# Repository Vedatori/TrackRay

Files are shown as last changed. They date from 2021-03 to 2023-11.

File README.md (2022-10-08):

# TrackRay [cz]
TrackRay je otevřená platforma robotického vozidla. Byl vyvinut pro [Letní technické soustředění 2020](http://wp.vedatori.com/pobytove-tabory/), které se věnovalo robotice, elektronice, programování a mechanické stavbě. Tábor pořádal spolek [Vědátoři](http://vedatori.com/), hlavními vývojáři byli Martin Ptáček, Martin Coufal a Marek Coufal. Dále se na vývoji podíleli Aleš Kraml, Petr Vávra, Max Matějka a Tomáš Sajdl. Jedná se o pásové vozidlo, které je schopné se pohybovat ve vnitřních prostorech, ale i v mírnějším terénu.

Větší mechanické části jsou vyřezány z překližky a plexiskla na lasové řezačce, spojovací díly a menší části jsou vytištěné na FDM 3D tiskárnách. Spojování dílů je řešeno pomocí šroubů M3. Vozidlo má poháněná zadní kola, k tomu je použit běžně dostupný motor s převodovkou. Všechna kola jsou uložena bez vypružení. Pásy byly navrženy tak, aby je bylo možné vytisknout na 3D tiskárně s již hotovým kloubovým spojením mezi jednotlivými segmenty - tím se minimalizoval počet spojů, které musí být při stavbě zhotoveny.

Elektronika je soustředěna na jednu DPS. Její součástí je i běžně neodebíratelný akumulátor 18650, nabíjecí obvod a indikátor nabití. Do desky se vsazuje mikrokontrolér ESP32-CAM. Ten zajišťuje WiFi konektivitu a ovládání periferií, jako je například LED matice 5x5 určená pro komunikaci s okolím nebo bzučák. TrackRay obsahuje gyroskop, pomocí něhož lze dosáhnout velmi přesné jízdy. Obraz z kamery připojené k mikrokontroléru je přenášen tak, aby ho viděl operátor. 

Vozidlo je možné opakovaně přeprogramovat a periferie jsou zvoleny tak, aby si na nich mohli uživatelé vyzkoušet mnoho úloh, které rozvedou jejich schopnosti algorimizace a programování. Je vytvořen firmware pro dálkové ovládání přes WiFi. Ten umožňuje buďto ovládání pomocí WiFi, kterou vytvoří samotné vozidlo, nebo je možné jej připojit k běžné domácí síti. Ovládání je přizpůsobeno pro chytrá zařízení, na nichž se zobrazí joystick pro jízdu a také obraz přenášený z kamery. Dále je možné zadat speciální příkazy do příkazového řádku, pomocí nich je možné ovládat některé z periferií.

K TrackRay bylo vyvinuto i dělo, které střílí airsoftové kuličky a dřevěné špalíky. Jeho autorem je Jan Cícha.

## Licence
* Obsah tohoto repozitáře mimo složku *Software* je sdílen pod licencí [Attribution-NonCommercial-ShareAlike 4.0 International (CC BY-NC-SA 4.0)](https://creativecommons.org/licenses/by-nc-sa/4.0/).
* Obsah složky *Software* je sdílen pod licencí [GNU Lesser General Public License v3.0](https://www.gnu.org/licenses/lgpl-3.0.en.html).

# TrackRay [en]
TrackRay is an open-source robotic vehicle platform. It was developed for the Robotic Summer Camp 2020 devoted to robotics, electronics, programming and mechanical assembly. The summer camp was organised by the [Vedatori](http://vedatori.com/) association. TrackRay was developed by Martin Ptáček, Martin Coufal and Marek Coufal as main developers, Aleš Kraml, Petr Vávra, Max Matějka and Tomáš Sajdl as associate developers. This vehicle uses tracks that make it capable of both indoor and outdoor driving.

Bigger mechanical parts were laser-cut from plywood and PMMA. FDM 3D printers were used to manufacture smaller parts. The vehicle is assembled using M3 bolts. The rear wheels are driven by standard TT motors, and the tracks are designed to be 3D printed in one piece with joints between each segment. 

All electonic components are placed on a single PCB. It contains 18650 battery with a charger circuit and a charge level indicator. An ESP32-CAM microcontroller is used for WiFi connectivity and peripherals control. A 5x5 LED matrix, a buzzer and a gyroscope are present on the TrackRay PCB. With camera on, it is possible to drive without direct visual contact.

With the used peripherals and option of reprogramming the vehicle it is suitable for gathering new programming skills. Remote control uses WiFi in two modes - if there is no WiFi present, it is possible to use WiFi created by the TrackRay microcontroller. It is also possible to connect TrackRay to a common WiFi network. The control screen is designed for smartphones and contains a joystick to control the robot. A camera stream and a command line to communicate with some of the peripherals.

An airsoft bullet blaster was developed as an optional accessory for the TrackRay. Jan Cícha is main developer of the blaster.

## License
* The contents of this repository excluding folder *Software* is shared under license [Attribution-NonCommercial-ShareAlike 4.0 International (CC BY-NC-SA 4.0)](https://creativecommons.org/licenses/by-nc-sa/4.0/).
* The contents of the folder *Software* is shared under license [GNU Lesser General Public License v3.0](https://www.gnu.org/licenses/lgpl-3.0.en.html).

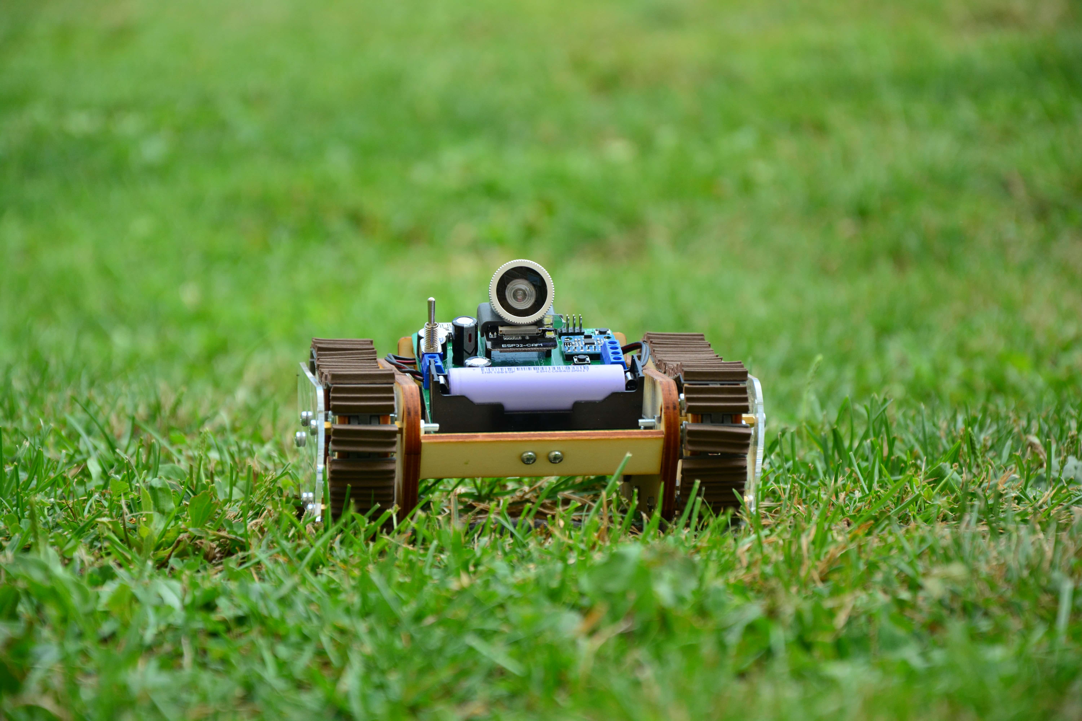
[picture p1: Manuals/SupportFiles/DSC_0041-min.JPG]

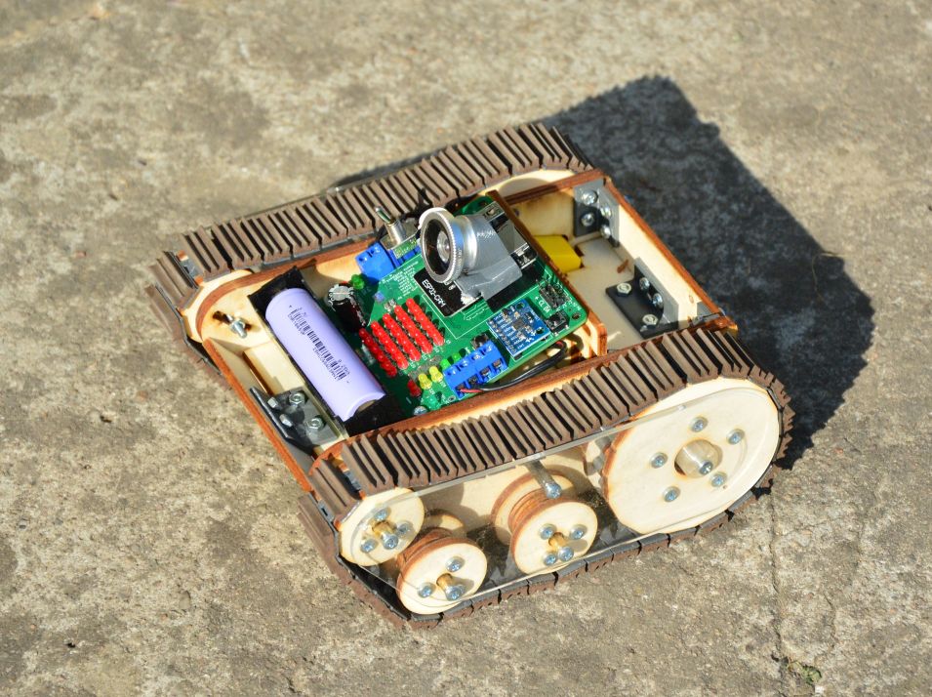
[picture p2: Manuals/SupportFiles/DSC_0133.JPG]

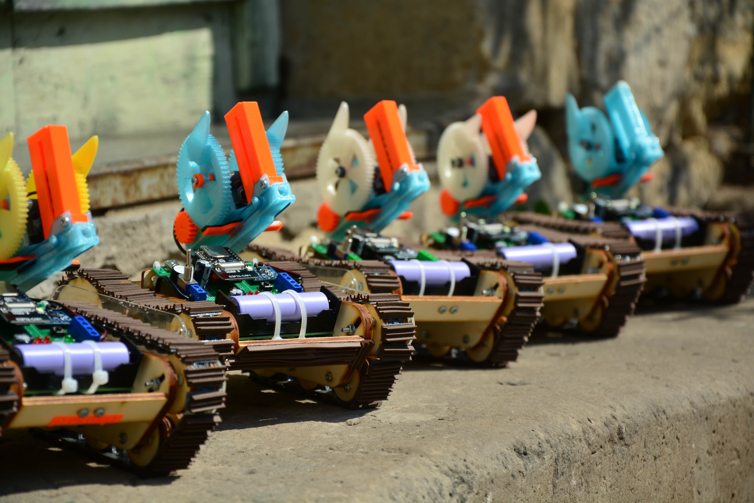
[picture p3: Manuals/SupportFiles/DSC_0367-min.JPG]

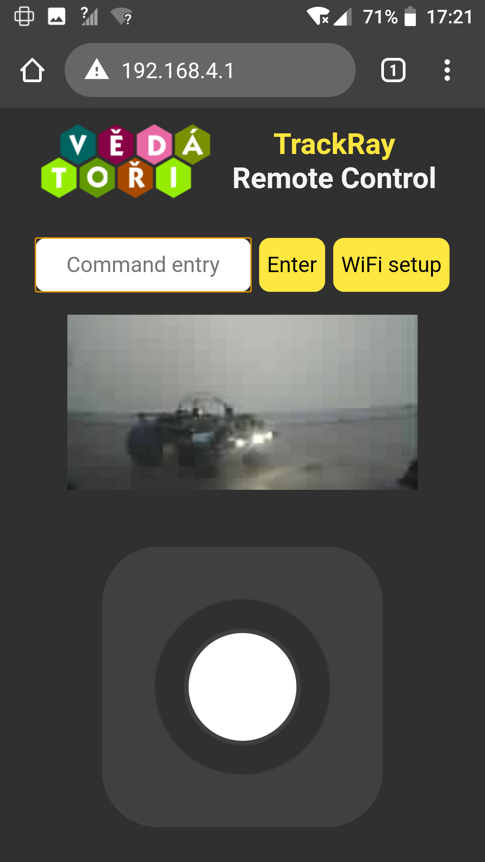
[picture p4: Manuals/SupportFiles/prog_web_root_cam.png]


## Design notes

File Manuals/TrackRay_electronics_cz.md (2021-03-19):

V tomto dokumentu je uveden návod na osazení desky plošných spojů. Část je osazena již z výroby SMD součástkami. Zbytek osazení je předmětem tohoto návodu.
Pro tento návod si uvedeme následující pojmy: DPS = PCB = deska - Deska Plošných Spojů.
Deska pro TrackRay je již z výroby osazena SMD (bezvývodovými) součástkami. THT (vývodové) se pájí následujícím způsobem:
* Součástku vkládáme ze strany, kde je naznačena silkscreenem (kde je bílou barvou natištěn její obrys).
* Součástku přitlačíme až k desce nebo co nejblíž.
* Součástku pájíme ze strany, na kterou trčí vývody.
* Vývody po zapájení zastřihneme.

# Obsah
* [Pájení LED](#LED)
* [Pájení malých součástek](#male)
* [Pájení větších součástek](#vetsi)
* [Vložení desky do robota a propojení](#finalizace)

## <a name = LED>Pájení LED</a>
**Potřebujeme:**
* 28x červená LED
* 4x zelená LED
* 2x žlutá LED

**Postup:**
<span style="color: red;">**POZOR: LED mají definovanou polaritu!**</span> U každé LED zkontrolujte, že kratší nožku vsouváte do čtveraté díry! 
1. Do desky vložte LED tak, aby barvy odpovídaly LED na obrázku. 
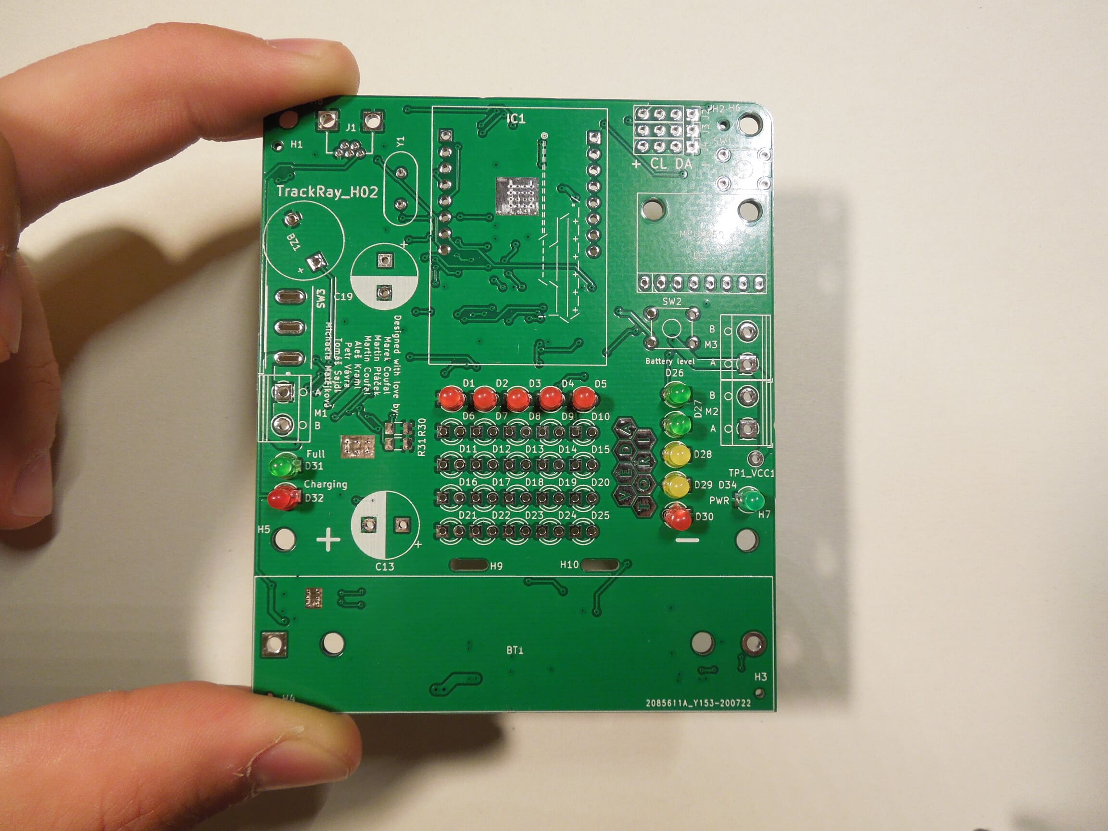
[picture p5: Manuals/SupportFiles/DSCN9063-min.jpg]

1. Na LED nasaďte pájecí přípravek. 
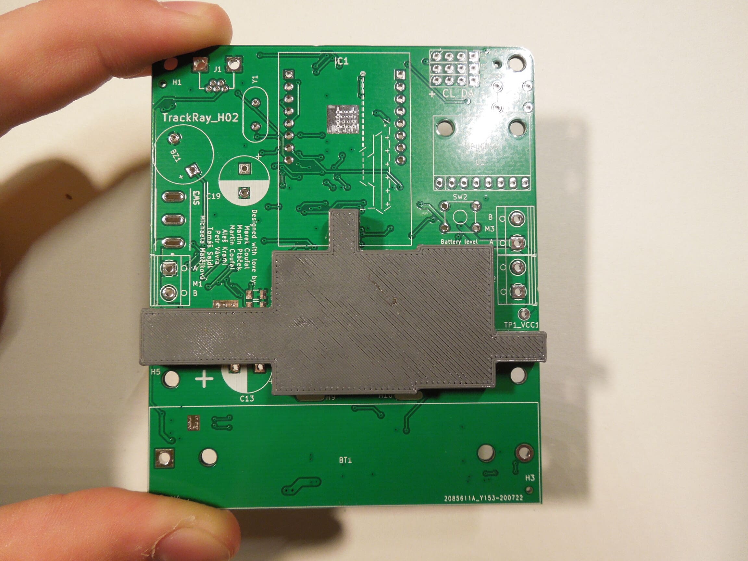
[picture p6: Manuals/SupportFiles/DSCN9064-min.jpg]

1. <span style="color: red;">**Před dalším postupem si nechte zkontrolovat desku vedoucím!**</span>
1. Vývody vsazených LED zapájejte. 
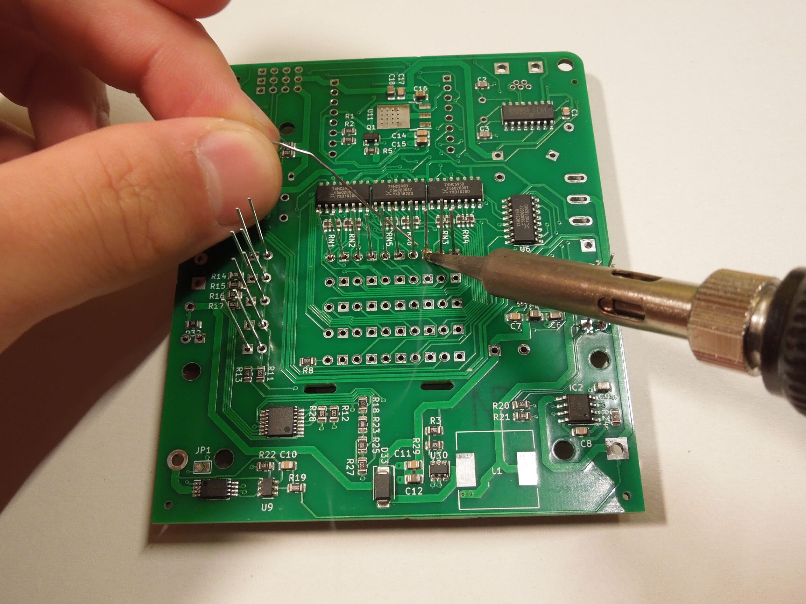
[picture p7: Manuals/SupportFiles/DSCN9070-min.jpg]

1. Do pole vložte další řadu LED. 
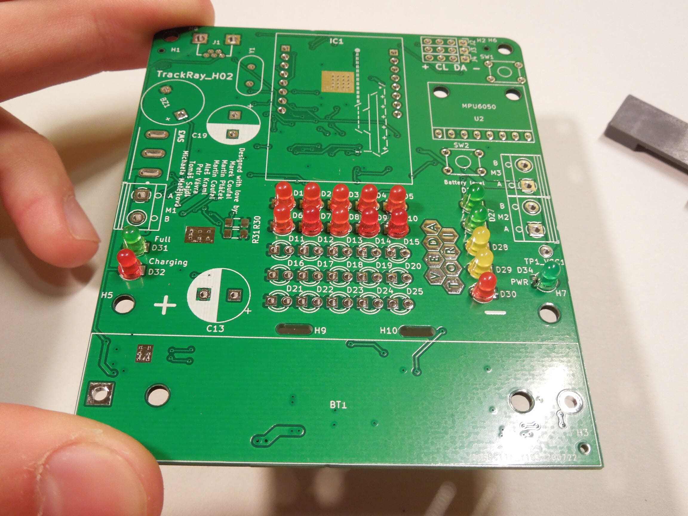
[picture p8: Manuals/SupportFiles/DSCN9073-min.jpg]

1. Nasaďte přípravek.
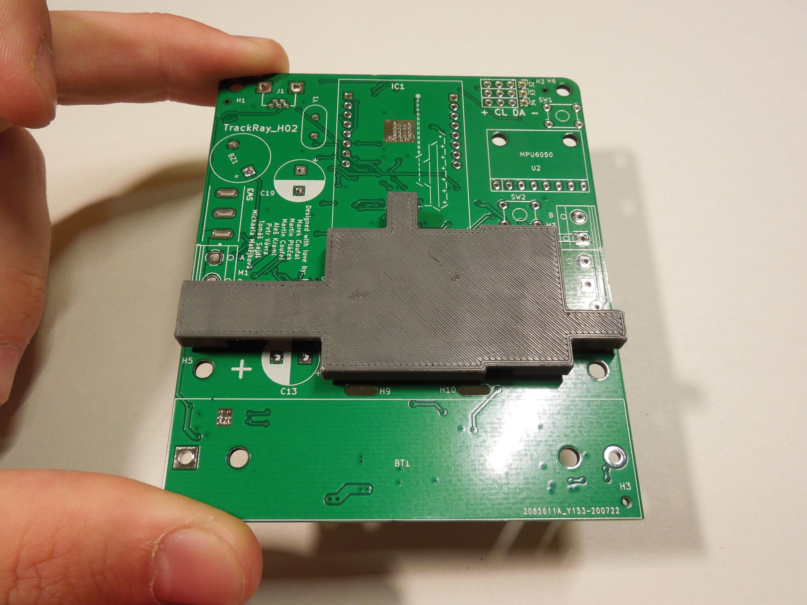
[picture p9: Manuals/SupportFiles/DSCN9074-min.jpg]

1. Zapájejte novou řadu LED.
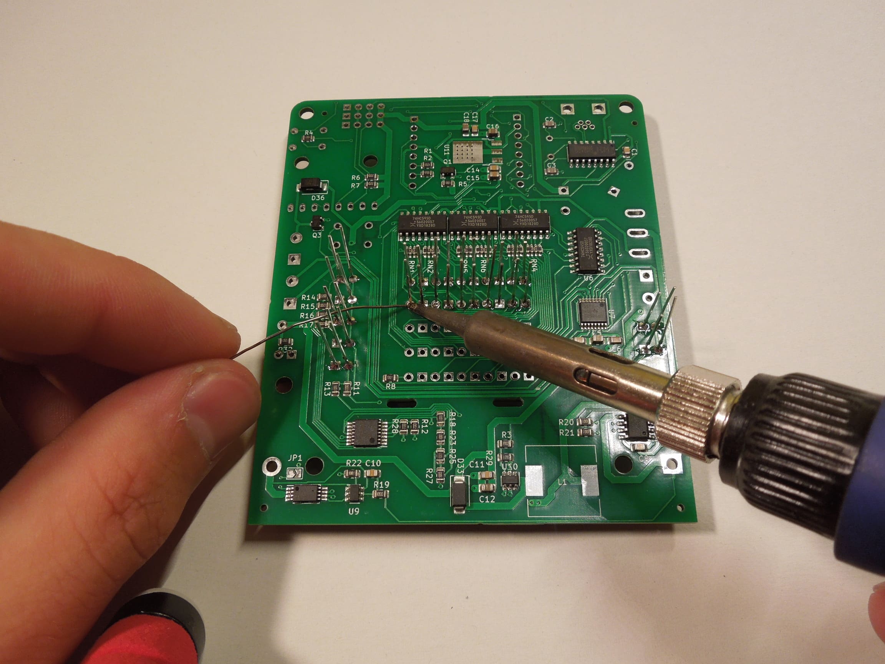
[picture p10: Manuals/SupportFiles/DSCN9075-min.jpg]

1. Tento postup opakujte, dokud nebudou zapájené všechny LED. 
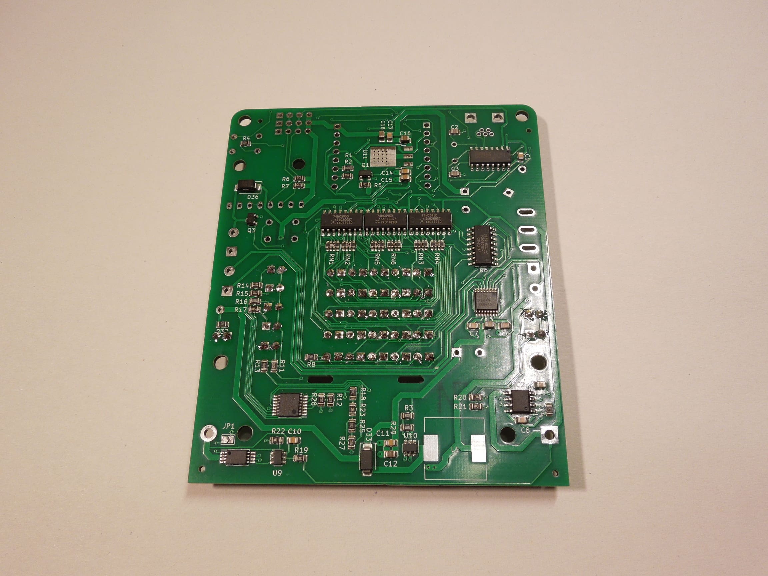
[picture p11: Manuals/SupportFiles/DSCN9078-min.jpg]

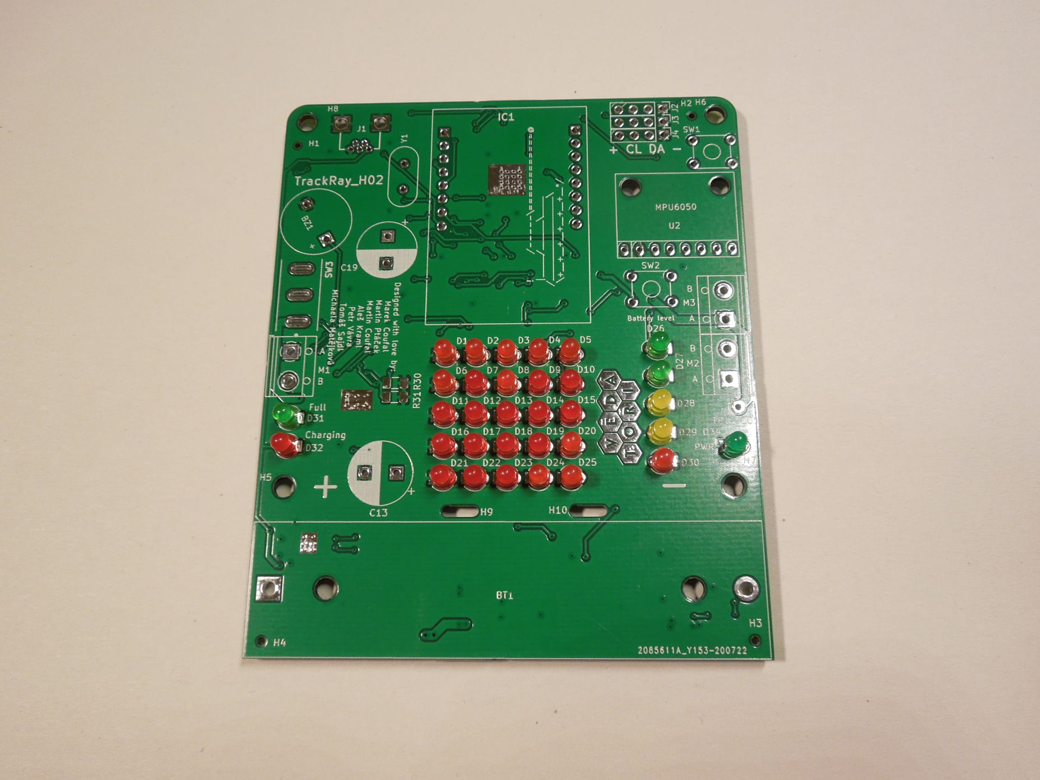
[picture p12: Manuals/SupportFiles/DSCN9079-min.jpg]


## <a name = male>Pájení malých součástek</a>
**Potřebujeme:**
* 2x SMD rezistor 0,22 Ohm
* 1x USB konektor
* 1x krystal
* 2x tlačítko

**Postup:**
1. Zapájejte *jumper JP1* na spodní straně desky a spojte cínem obě jeho plošky.
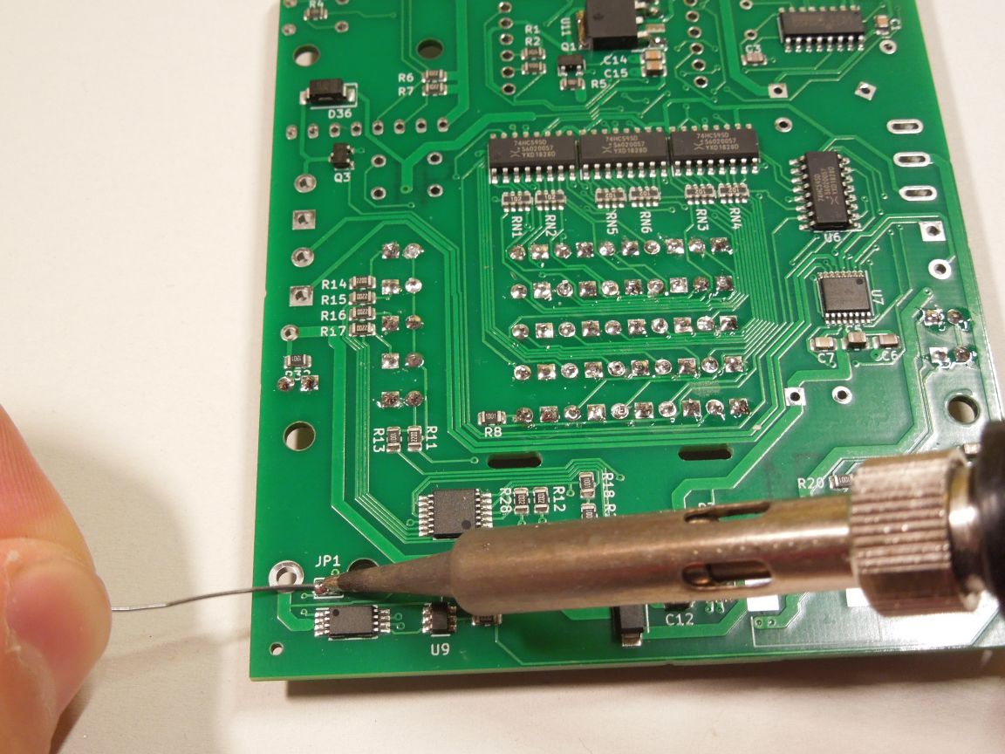
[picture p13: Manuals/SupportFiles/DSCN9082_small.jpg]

1. Zapájejte SMD rezistory. Na jednu pájecí plošku naneste pájku.
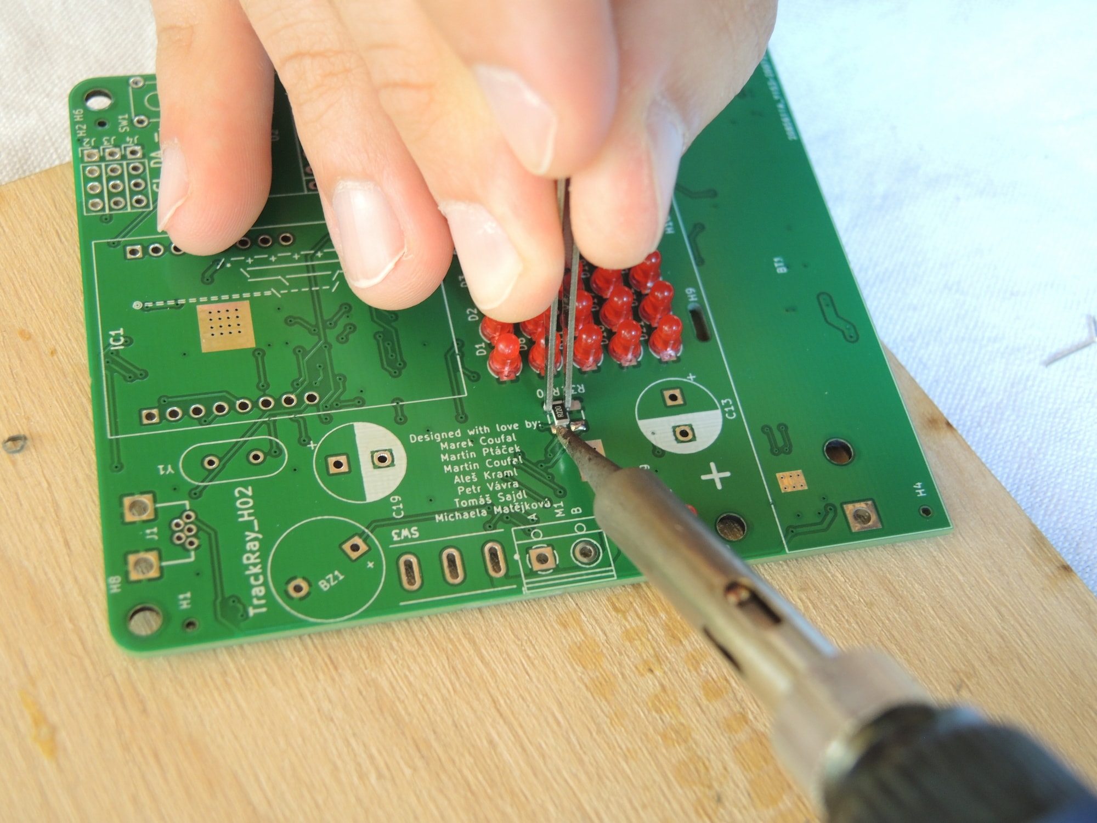
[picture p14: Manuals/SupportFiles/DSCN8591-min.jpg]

1. Přiložte SMD rezistor. Roztavte předem nanesený cín a tím připájejte rezistor. Poté zapájejte druhý vývod rezistoru. Stejným způsobem zapájejte i druhý rezistor.
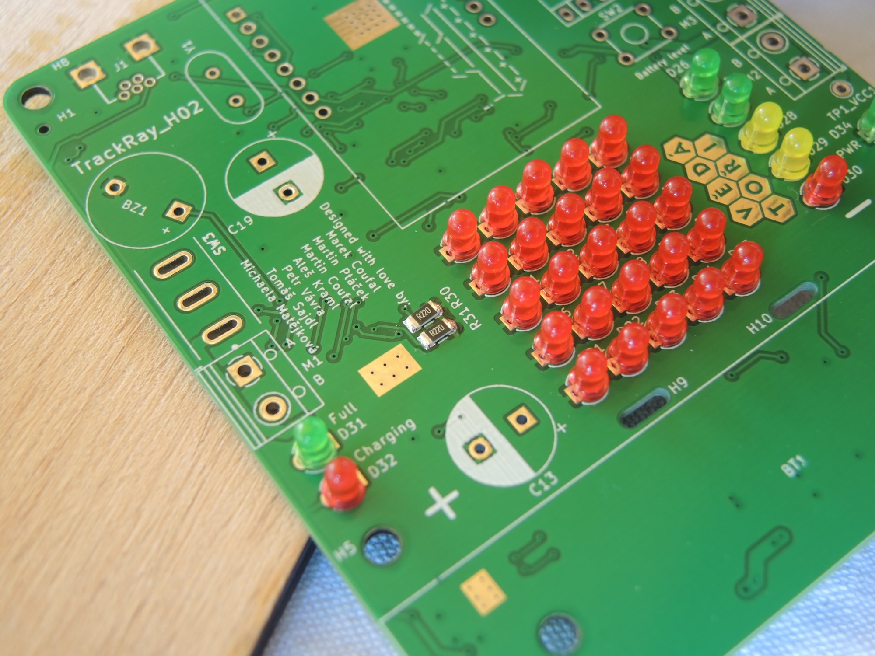
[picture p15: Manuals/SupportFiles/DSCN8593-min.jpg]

1. Vložte USB konektor na místo H8. Skrz desku musí vyčnívat tenké vývody i tlusté fixovací vývody.
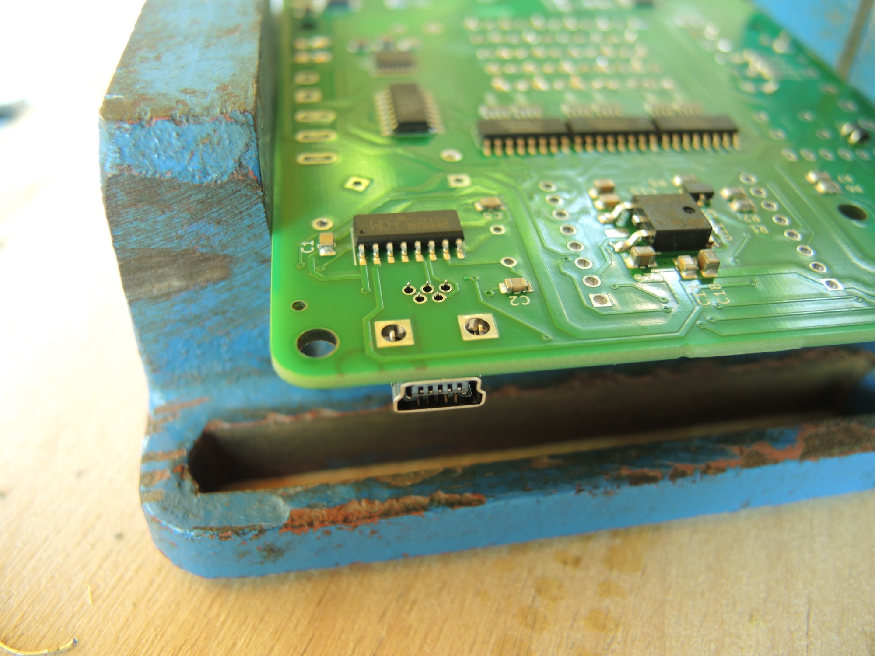
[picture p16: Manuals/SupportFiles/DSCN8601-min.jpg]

1. Tlusté i tenké vývody připájejte klasicky zespodu, jak je popsáno v úvodní části návodu. Tlusté vývody je možné zapájet z obou stran. 
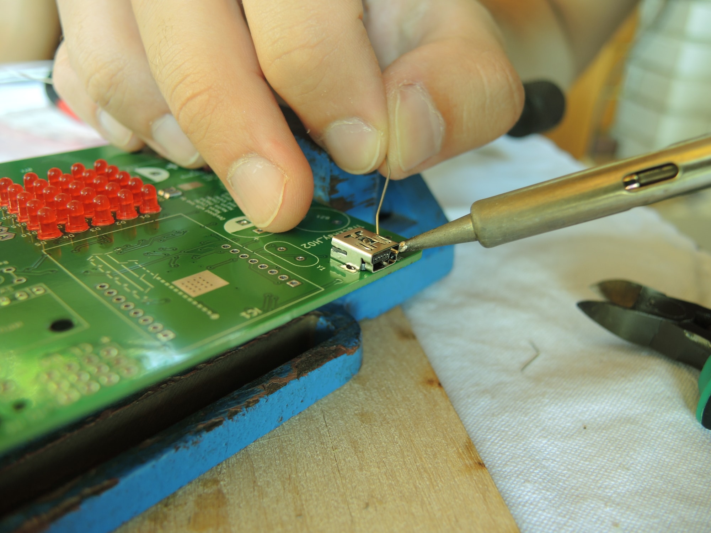
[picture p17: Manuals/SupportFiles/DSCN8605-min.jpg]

1. Na místo Y1 zapájejte krystal.
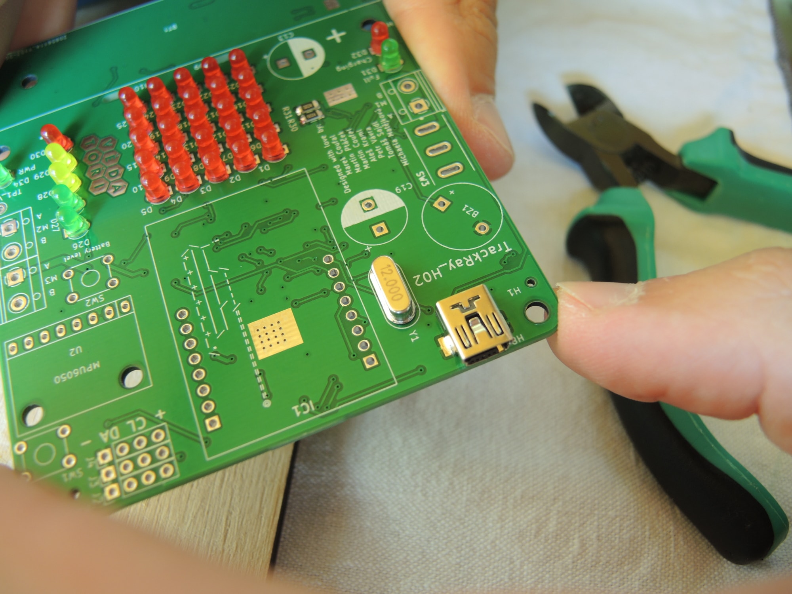
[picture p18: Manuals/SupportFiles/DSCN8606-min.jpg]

1. Na místa SW1 a SW2 zapájejte tlačítka. 
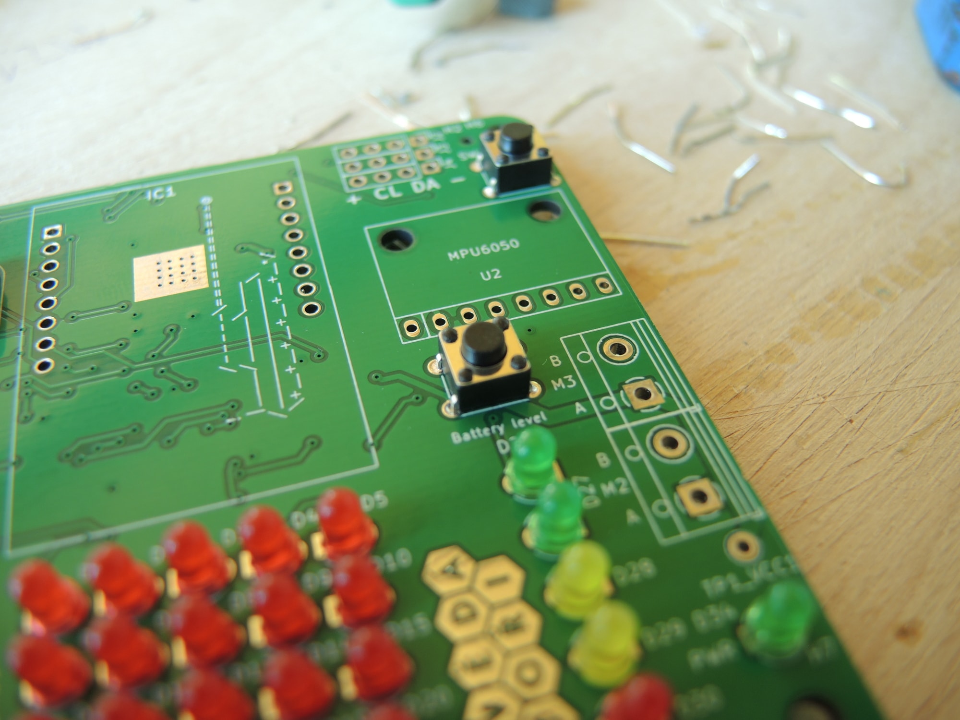
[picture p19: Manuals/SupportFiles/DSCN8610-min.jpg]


## <a name = vetsi>Pájení větších součástek</a>
**Potřebujeme:**
* 0,5x dutinková lišta
* 3x terminal block
* 2x elektrolytický kondenzátor 1000 uF
* 1x páčkový přepínač
* 1x držák baterie
* 1x gyroskop

**Postup:**
1. Naměřte si dutinkovou lištu tak, abyste si vyrobili 2x 8pin dutinky. Dutinky oddělte kleštěmi vždy uprostřed dalšího pinu, ten se zničí.
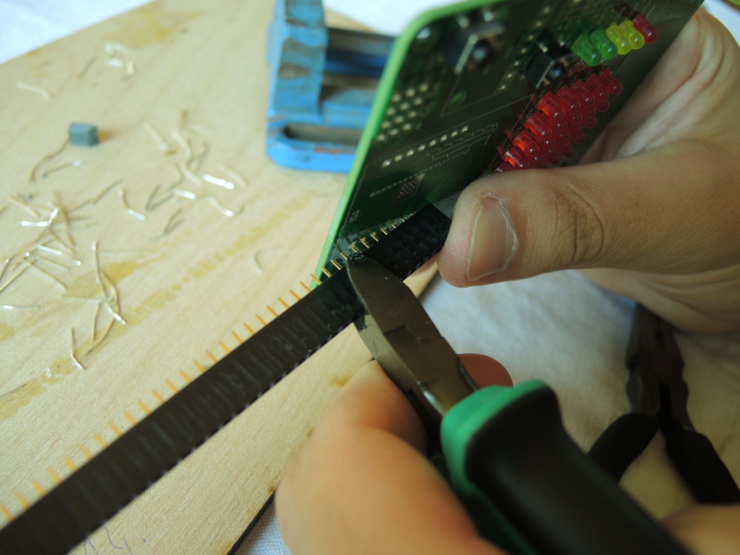
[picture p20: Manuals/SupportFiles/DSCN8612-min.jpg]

1. Nadělené dutinky začistěte nožem nebo kleštěmi tak, aby nebyly viditelné zbytky odstřihnutého pinu.
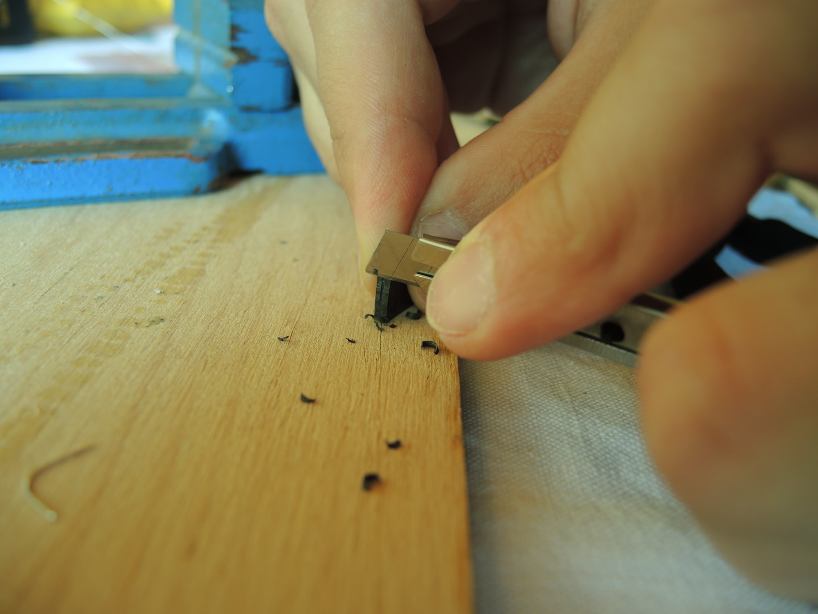
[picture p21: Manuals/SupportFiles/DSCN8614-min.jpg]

1. Vložte dutinku do desky k umístění IC1, zapájejte jeden pin. Poté zkontrolujte, jestli není dutinka nakřivo. Dorovnejte a zapájejte ostatní piny.
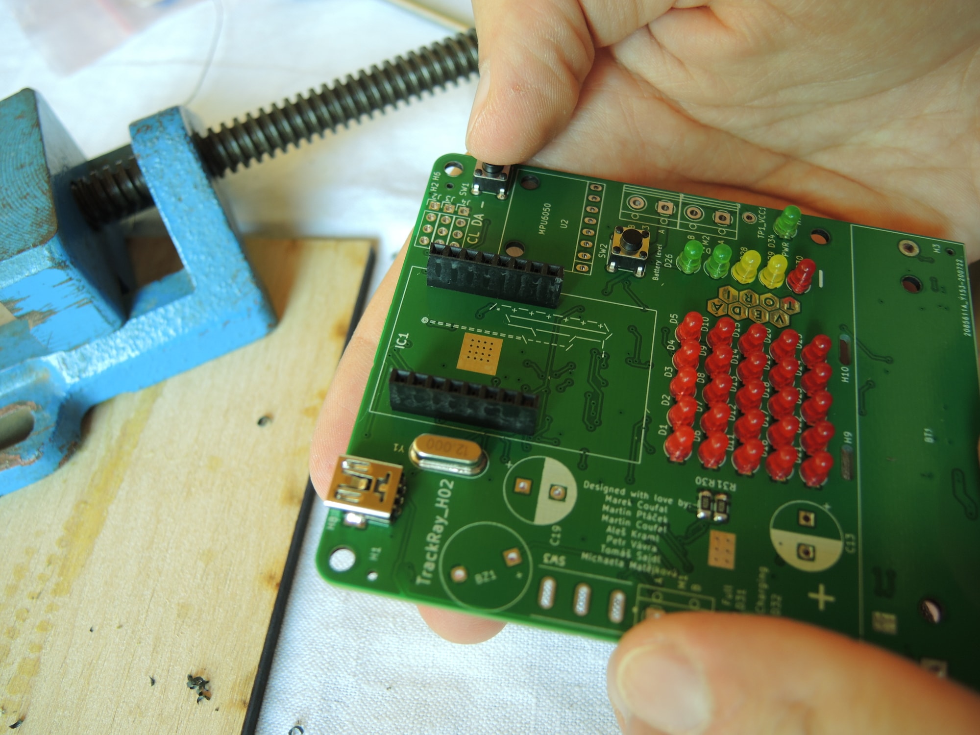
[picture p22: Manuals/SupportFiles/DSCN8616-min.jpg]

1. Zapájejte buzzer do místa s označením BZ1. Pozor na polaritu, delší vývod (u symbolu plus na etiketě buzzeru) musí být umístěn do otvoru označeným symbolem +. 
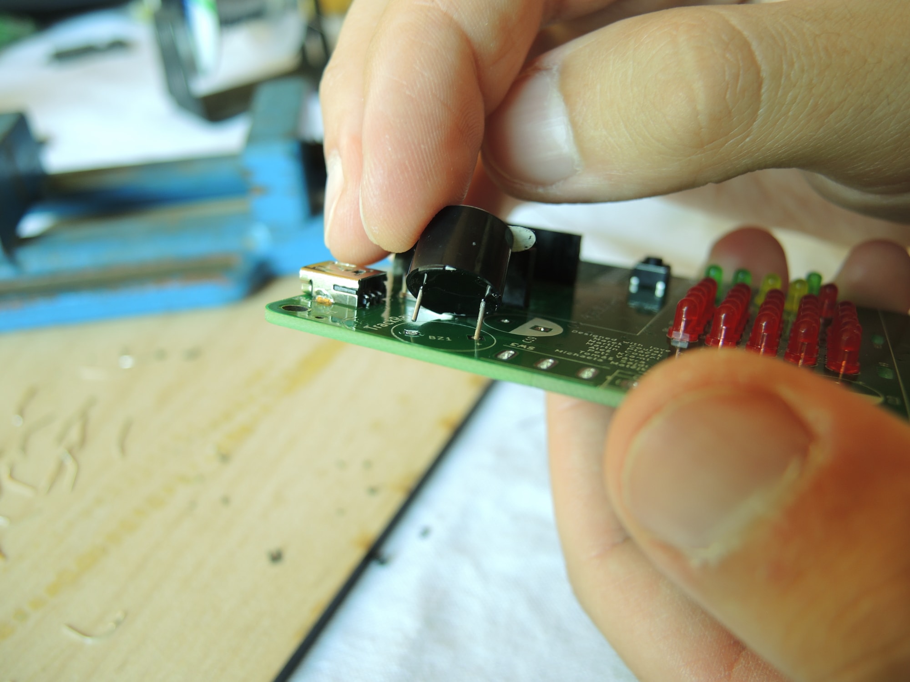
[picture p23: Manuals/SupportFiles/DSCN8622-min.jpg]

1. Nasuňte do sebe dva terminal blocky. 
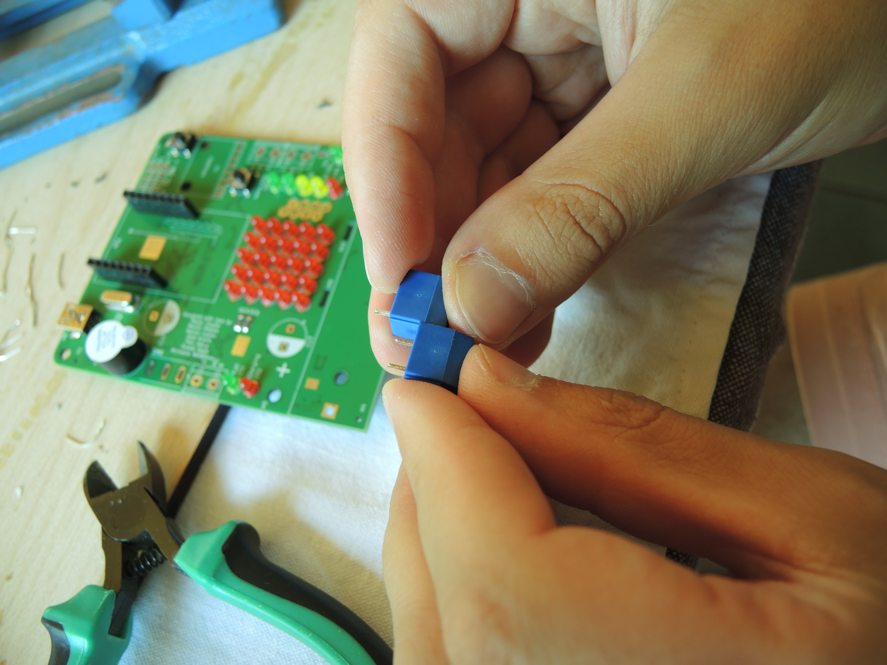
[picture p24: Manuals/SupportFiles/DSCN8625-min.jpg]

1. Zapájejte je na místa označená M2 a M3 tak, aby otvory pro kabely směřovaly ven z desky. 
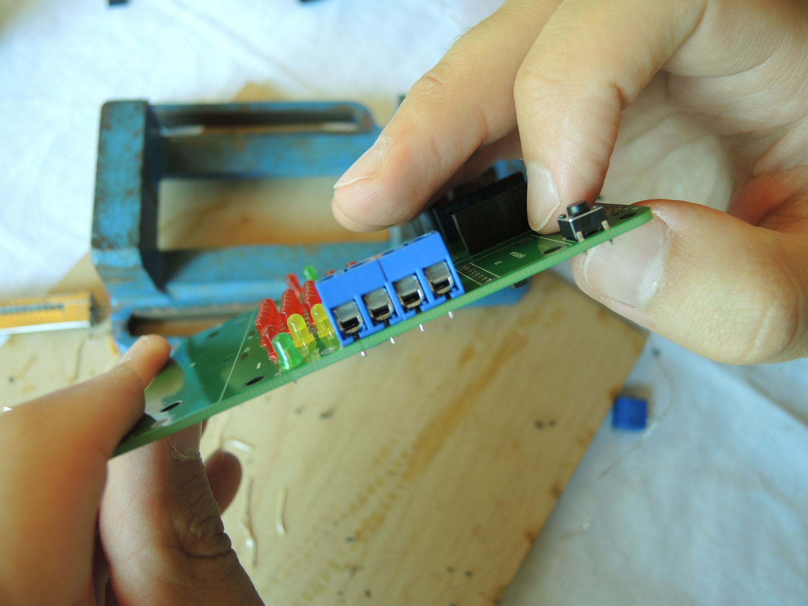
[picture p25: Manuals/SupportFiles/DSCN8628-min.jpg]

1. Zapájejte jeden terminal block na místo M1 tak, aby otvory pro kabely směřovaly ven z desky. 
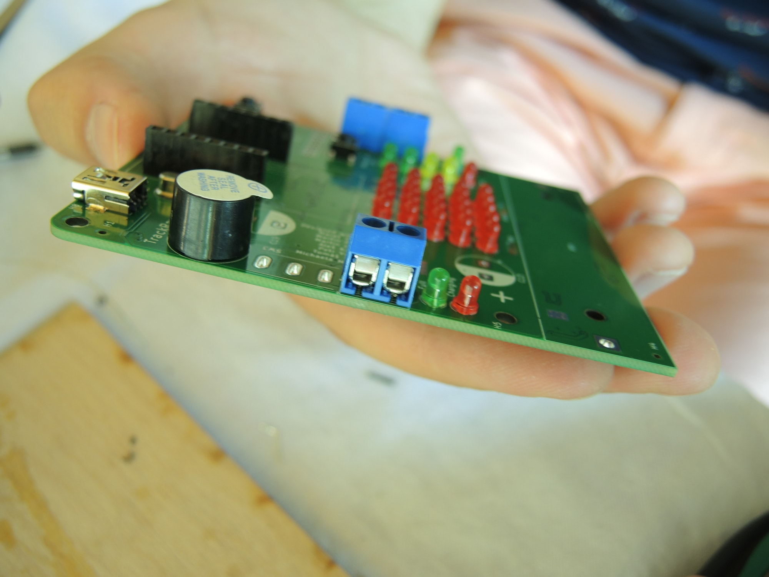
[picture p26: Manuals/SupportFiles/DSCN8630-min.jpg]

1. Na místa označená C13 a C19 zapájejte elektolytické kondenzátory. Pozor na polaritu, delší vývod musí směřovat do otvoru, u kterého je smybol + a jeho okolí není zabarvené bílou barvou.
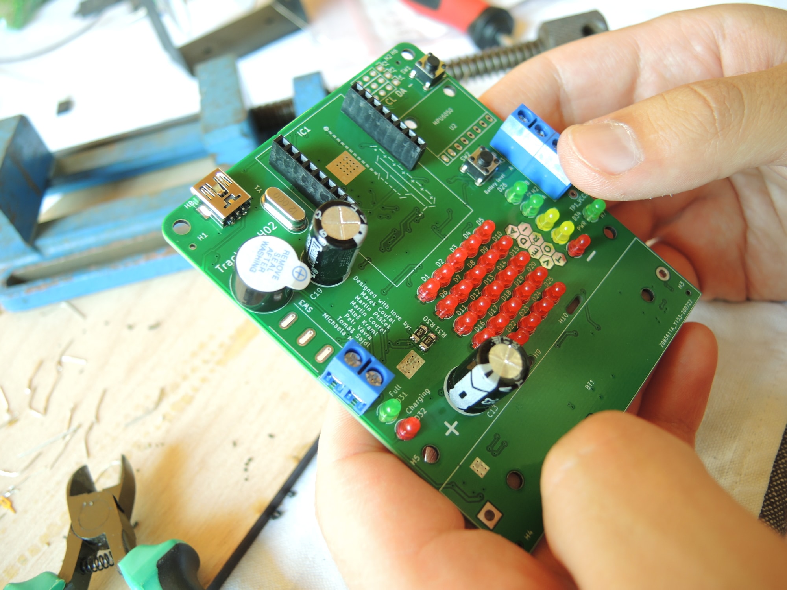
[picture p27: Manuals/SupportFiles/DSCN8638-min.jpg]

1. Na místo označené SW3 vložte páčkový přepínač. Zapájejte. Při pájení dbejte na to, aby byl kolmo k desce, po připájení je obtížné ho narovnat. 
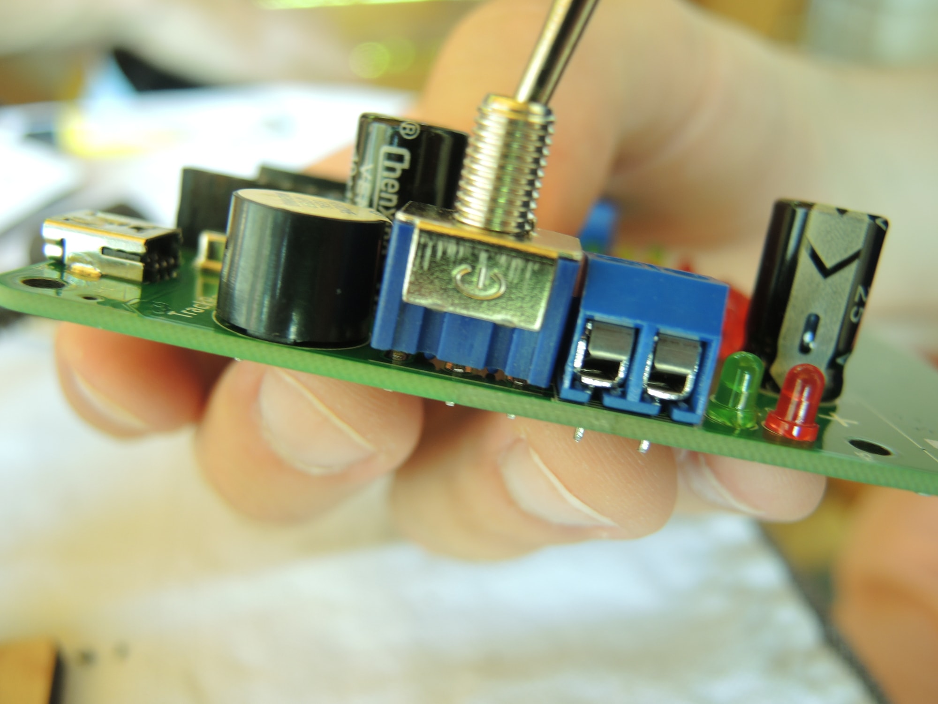
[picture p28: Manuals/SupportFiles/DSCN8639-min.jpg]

1. Na místo označené BT1 připájejte držák baterie. Symbol + na desce musí odpovídat symbolu + na držáku baterie. 

1. Napájejte kolíkovou lištu na gyroskop. Nejdříve zapájejte jeden pin a poté lištu srovnejte, aby s deskou gyroskopu svírala pravý úhel. Poté zapájejte ostatní piny kolíkové lišty.

1. Zapájejte gyroskop do desky na místo označené MPU6050. 


## <a name = Finalizace>VLožení desky do robota a propojení</a>
**Potřebujeme:**
* 2x šroub M3x8
* 2x velký upínací pásek
* 2x malý upínací pásek

**Postup:**
1. Baterii do robota vsazuje vedoucí!!! Po jejím vsazení ji přichyťte pomocí velkých upínacích pásků, jejich konce zastřihněte kleštěmi.


1. Desku vložte do robota. Pomocí dvou šroubů M3x8 desku zašroubujte do držáků na robotovi skrz díry H5 a H7 na desce. 

1. Do terminal blocků M1 a M2 připojte kabely od motorů. Kabel s červeným proužkem bude vždy připojen do otvoru blíže baterii. Zašroubujte.

1. Na horní straně desku připevněte skrz díry H1 a H6 pomocí upínacích pásků. Zcela je nedotahujte. Konce zastřihněte. 



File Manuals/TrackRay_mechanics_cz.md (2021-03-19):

V tomto dokumentu je uveden návod na sestavení mechanických dílů vozítka TrackRay. Část mechanických dílů je vyrobena technologií 3D tisku, část je vyřezána z překližky a plexiskla pomocí laseru, dalším dílem je osazená deska plošných spojů, ostatní součástky tvoří běžně dostupný spojovací materiál. 

___
# Obsah
* [Příprava překližkových dílů](#preklizka)
* [Sestavení velkých kol](#kolo)
* [Sestavení malých kol](#kolecka)
* [Sestavení bočnic #1](#bocnice1)
* [Sestavení bočnic #2](#bocnice2)
* [Kompletace šasi](#sasi)
* [Polepení pásů](#pasy1)
* [Slepení pásů](#pasy2)
* [Nasazení pásů](#pasy3)
* [Kamera](#kamera)
___

## <a name = preklizka>Příprava překližkových dílů</a>
**Nástroje:**
* Smirek

**Postup:**
1. Obruste smirkem všechny nedořezky. 


## <a name = kolo>Sestavení velkých kol</a>
**Potřebné díly:**


* 2x kolo neozubené velké z překližky
* 1x kolo ozubené velké z překližky
* 1x kolo ozubené velké 3D tisk
* 5x matice M3
* 5x šroub M3x22

**Nástroje:**
* Křížový šroubovák
* Maticový klíč



**Postup:**
1. Provléct šroub skrz díru pod malou dírkou. Otočit na opačnou stranu. 

    
1. Navléct ozubené kolo z překližky. Malé dírky musí padnout na sebe. 

    
1. Navléct 3D tištěný díl tak, aby výstupek pro zastrčení osy směřoval směrem od dřevěných dílů. 

    
1. Navléct neozubené kolo z překližky. 

    
1. Zašroubovat matku. Neutahovat.

    
1. Doplnit zbylé šrouby a matky. Díly vystředit vůči sobě. Všechny matky utáhnout maticovým klíčem. 

    
1. Celý postup zopakujeme pro druhé kolo.

    
## <a name = kolecka>Sestavení malých kol</a>
**Potřebné díly:**


* 2x kolo neozubené malé z překližky
* 2x kolo neozubené maličké z překližky
* 1x vymezovač kola 3D tisk
* 3x matice M3
* 3x šroub M3x22

**Nástroje:**
* Křížový šroubovák
* Maticový klíč

**Postup:**
1. Provléct šroub skrz malé kolo. 

    
1. Navléct maličké kolečko.

    
1. Navléct další maličké kolečko. 

    
1. Doprostřed vložit vymezovač kola z 3D tisku. 

    
1. Navléct malé kolo. 

    
1. Zašroubovat matku. Neutahovat. 

    
1. Doplnit zbylé šrouby a matky. Díly vystředit vůči sobě. Všechny matky utáhnout. 

    
1. Stejným postupem sestavit zbylá kola. Celkově jich bude 6. 

    

## <a name = bocnice1>Sestavení bočnic #1</a>
**Potřebné díly:**
* 2x bočnice z překližky
* 2x plastový držák z 3D tisku
* 4x matice M3
* 4x šroub M3x10

**Nástroje:**
* Křížový šroubovák
* Maticový klíč
* Klíč na distanční sloupky (šedý)



**Postup:**
1. Rozchystat součástky podle nákresu. 

    
1. Umístit držák na Bočnici 2. 

    
1. Skrz Bočnici 2 provléct šrouby a utáhnout matky. 

    
1. Postup zopakujte pro Bočnici 1. 

    

## <a name = bocnice2>Sestavení bočnic #2</a>
**Potřebné díly:**

Díly jsou uvedeny postupně pro každý krok. 

**Nástroje:**
* Křížový šroubovák
* Maticový klíč
* Klíč na distanční sloupky (šedý)

**Postup:**

*Postup je předveden na Bočnici 2*
1. Odlepit z obou stran plexiskla ochranou folii. 

    
1. Rozchystat součástky podle nákresu. 

    
1. Prošroubovat šroub M3x10 skrz bočnici z plexiskla do distančního sloupku M3x30. 

    
1. Protáhnout šrouby M3x40 skrz bočnici z plexiskla. 

    
1. Na šrouby našroubovat distanční sloupky M3x10. Dotáhnout pomocí klíče na distanční sloupky. 

    
1. Přidat šroub M3x45 do pohyblivé drážky a našroubovat distanční sloupek. Nedotahovat, nechat volně. 

    
1. Nasadit kolečka. 

    
1. Našroubovat distanční sloupky. 

    
1. Dotáhnout distanční sloupky u šroubů M3x40 (jsou v kulatých dírách, ne v pohyblivé drážce). 

    
1. Zatlačte matku šroubovákem do dílu z 3D tisku. 

    [alt](SupportFiles/DSCN8417.JPG)
1. Připravte díly dle obrázku. 

    
1. Připevněte šroubem M3x12. 

    
1. Nasuňte motor do otvoru. Zkontrolujte, že máte vše ve shodě s obrázkem. 
    * Bočnici s 3D tištěným dílem.
    * Kabel jde na opačnou stranu bočnice. 
    * Uštípnutý bílý plast na motoru.

    
1. Zkontrolujte, že máte ve shodě s obrázkem. 

    
1. Nasaďte 3D tištěný díl. Obraťte na druhou stranu. 

    
1. Vložte šrouby M3x25 hlavou k motoru. Obraťte na druhou stranu. 

    
1. Přidejte matky a dotáhněte tak, aby nepraskl plastový kryt motoru.

    
1. Protáhněte šroubky M3x10 hlavou K 3D tištěnému držáku. Obraťte na druhou stranu. 

    
1. Přišroubujte matky a utáhněte. 

    
1. Pro upevnění motoru si připravte tyto díly. 

    
1. Vložte podložku z 3D tisku pod očko od motoru. Obraťte na opačnou stranu.  

    
1. Protáhněte šroub M3x16 s vnořenou hlavou. 

    
1. Našroubujte matku a utáhněte. Hlava šroubu by měla být úplně nebo skoro vyrovnaná s plochou bočnice.

    
1. Pro upevnění hnacího kola budete potřebovat tyto díly. Nasaďte kolo na bílý plast motoru. 

    
1. Prošroubujte středem kola černý vrut 2,2x10 a utáhněnte. 

    
1. Protáhněte kabely od motoru na opačnou stranu bočnice. 

    
1. Pro připevnění L - držáku korby budete potřebovat tyto díly. 

    
1. Umístěte držák a protáhněte šrouby M3x10. Otočte na druhou stranu. 

    
1. Přišroubujte matky, utáhněte. 

    
1. Přiložte obě části bočnice. 

    
1. Přichystejte 3 matky M3 a šroub M3x10. Šroub namontujte a utáhněte.

    
1. Matku v posuvné drážce nedotahujte, kolo nechte volně pohybovat. Další matky utáhněte.

    
1. Stejným postupem zkompletujte druhou bočnici. 

    

## <a name = sasi>Kompletace šasi</a>

**Potřebné díly:**


* Zbývající díly z překližky
* 20 matic
* 20 šroubů M3x8

**Nástroje:**
* Křížový šroubovák
* Maticový klíč

**Postup:**
 
 *Šroubovat a utahovat.* **Dodržujte umístění hlav a konců šroubů podle fotek.**

1. Přišroubujte šasi k bočnici. 

    

    

    

    
1. Stejně na druhé straně. 

    
1. Připevněte L - držák z 3D tisku.

    
1. Připevněte zadní kryt korby.

    
1. Připevněte šikmý držák z 3D tisku (tento držák není pod úhlem 90°).

    
1. Připevněte přední kryt korby. 

    
1. Připevněte L - držák z 3D tisku na přepážku z překližky.

    
1. Spojte přepážku s šasi.

    
1. Nachystejte 3D tištěně držáky desky plošných spojů, 2 šrouby M3x8 a 4 matky M3. Matky vložte do 3D tištěných dílů.

    
1. Spojte držáky s šasi.

    

## <a name = pasy1>Polepení pásů</a>

**Potřebné díly:**
* 4x vytištěný kus pásu
* 2 m těsnění do oken
 
**Nástroje:**
* štípací kleště / nůžky
* 3D tištěné měřidlo



**Postup:**

1. Nastříhejte z pryžové pásky nálepku na každý článek pásu. Bude potřeba 72 kusů těsnění. Použijte 3D tištěné měřítko pro odměření velikosti článků. 

    
1. Každý článek pásů polepte. Na těsnění je pod ochrannou fólií samolepící vrstva.

    

## <a name = pasy2>Slepení pásů</a>

**Potřebné díly:**
* 4x 3D tištěné pásy
* kus filamentu
 
**Nástroje:**
* lepidlo na plasty
* nůžky
* kleště
* pravítko

**Postup:**

1. Nastříhejte z filamentu 4 kusy po 0,9 cm.

    
1. Pomocí kleští vsuňte kus filamentu na spojnici mezi pásy.

     
1. Zalepte kus filamentu z obou stran. **Pozor:** Použijte malé množství lepidla, aby se nedostalo do kloubů pásu.

    
1. Lepidlo nechte zaschnout  min. 20 minut. Po tuto dobu s pásy výrazně nehýbejte, nesnažte se je nasadit na robota!

## <a name = pasy3>Nasazení pásů</a>

**Potřebné díly:**
* 2x zkompletované pásy
* 1x zkompletované šasi

**Nástroje:**
* Maticový klíč
* Klíč na distanční sloupky (šedý)
* Šroubovák

**Postup:**

1. Nachystejte potřebné díly. 

    
1. Postupně nasaďte pásy. 

    

    

    
1. Vypněte pás a dotáhněte pohyblivé kolo. 

    

    

## <a name = elektronika>Elektronika</a>

[*Pájení je v samostatném návodu.*](TrackRay_electronics_cz.md)

## <a name = Kamera>Kamera</a>

**Potřebné díly:**
* 1x držák kamery z 3D tisku
* 1x čočka fish-eye
* 1x obdélník stříbrné pásky

**Nástroje:**
* Lepidlo



**Postup:**
1. Našroubujte čočku. **Pozor**: Pohlídejte, aby závit čočky zajel přesně do závitu držáku.

    
1. Naneste malou kapku lepidla na držák kamery.

    
1. Odlepte obdélníkový kus stříbrné pásky z podkladového papírku.

    
1. Přilepte zrcátko.

    
1. Před dalším postupem zavolejte vedoucího.
1. Otevřete konektor pro kameru na ESP-CAM.

    
1. Zasuňte kameru do konektoru na ESP-CAM.

    
1. Kameru namiřte a částečně zasuňte do díry v držáku kamery.

    
1. Držák kamery opatrně nacvakněte shora na ESP-CAM. **Pozor**: Přední část musí být zarovnána s koncem kolíkové lišty jak vyznačuje šipka.

    
1. Zasaďte ESP32 do desky plošných spojů. **Pozor**: dbejte na správnou orientaci a zarovnání kolíkových lišt.



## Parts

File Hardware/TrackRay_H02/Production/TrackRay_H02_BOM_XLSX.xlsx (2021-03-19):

Comment | Designator | Footprint | LCSC Part Number
18650 | BT1 | Battery:BatteryHolder_MPD_BH-18650-PC2
Buzzer | BZ1 | Buzzer_Beeper:Buzzer_12x9.5RM7.6
100n | C1,C10,C8,C14,C17,C11 | Capacitor_SMD:C_0805_2012Metric | C49678
470u | C19,C13 | Capacitor_THT:CP_Radial_D10.0mm_P5.00mm
22p | C3,C2 | Capacitor_SMD:C_0805_2012Metric | C1804
10u | C5,C9,C15,C18,C16,C12 | Capacitor_SMD:C_0805_2012Metric | C15850
2u2 | C6 | Capacitor_SMD:C_0805_2012Metric | C49217
10n X7R 16V! | C7 | Capacitor_SMD:C_0805_2012Metric | C1710
LED | D1,D2,D3,D4,D5,D6,D7,D8,D9,D10,D11,D12,D13,D14,D15,D16,D17,D18,D19,D20,D21,D22,D23,D24,D25 | LED_THT:LED_D3.0mm
LED_YELLOW | D27,D28 | LED_THT:LED_D3.0mm
LED_RED | D29,D30,D32 | LED_THT:LED_D3.0mm
LED_GREEN | D31,D26 | LED_THT:LED_D3.0mm
LED_PWRON | D34 | LED_THT:LED_D3.0mm
D_Schottky | D36,D33 | Diode_SMD:D_SMA | C8678
MountingHole_JLCPCB | H1,H2,H3,H4 | TrackRay_Library:JLCPCB_ToolingHole
MountingHole | H5,H6,H7,H8 | MountingHole:MountingHole_3.2mm_M3
MountingHole_ZIPTie | H9,H10 | TrackRay_Library:ZIP_Tie_Slot_Hole
ESP32-CAM | IC1 | TrackRay_Library:ESP32-CAM
TP4056 | IC2 | Package_SO:SOIC-8-1EP_3.9x4.9mm_P1.27mm_EP2.514x3.2mm_ThermalVias | C16581
USB_B_Mini | J1 | TrackRay_Library:USB_MINIB
Conn_01x04_Male | J2,J3,J4 | Connector_PinHeader_2.54mm:PinHeader_1x04_P2.54mm_Vertical
Jumper_2_Open | JP1 | Jumper:SolderJumper-2_P1.3mm_Open_TrianglePad1.0x1.5mm
22uH | L1 | Inductor_SMD:L_12x12mm_H6mm
Motor_DC | M1,M2,M3 | TerminalBlock_RND:TerminalBlock_RND_205-00012_1x02_P5.00mm_Horizontal
Q_NMOS_GSD | Q1,Q3 | Package_TO_SOT_SMD:SOT-23 | C20917
FS8205A | Q2 | Package_SO:TSSOP-8_4.4x3mm_P0.65mm | C16052
220R | R11,R14,R15,R16,R17 | Resistor_SMD:R_0805_2012Metric | C17557
10K | R12,R28 | Resistor_SMD:R_0805_2012Metric | C17414
100R | R19 | Resistor_SMD:R_0805_2012Metric | C17408
470R | R2,R1 | Resistor_SMD:R_0805_2012Metric | C17710
1K2 | R24,R32 | Resistor_SMD:R_0805_2012Metric | C17379
100K | R27 | Resistor_SMD:R_0805_2012Metric | C17407
3K6 | R29 | Resistor_SMD:R_0805_2012Metric | C18359
39K | R3 | Resistor_SMD:R_0805_2012Metric | C25826
0R22 | R30,R31 | Resistor_SMD:R_1206_3216Metric
1K | R5,R4,R8,R22,R21,R20,R13,R18,R23,R25 | Resistor_SMD:R_0805_2012Metric | C17513
2K2 | R6,R7 | Resistor_SMD:R_0805_2012Metric | C17520
R_Pack04 | RN1,RN3,RN4,RN5,RN6,RN2 | Resistor_SMD:R_Array_Convex_4x0603 | C20197
SW_DPST | SW1,SW2 | Button_Switch_THT:SW_TH_Tactile_Omron_B3F-10xx
MT-102 | SW3 | TrackRay_Library:TE_A101SYCQ04
TestPoint | TP1_VCC1 | TestPoint:TestPoint_THTPad_D2.0mm_Drill1.0mm
CH340G | U1 | Package_SO:SOIC-16_3.9x9.9mm_P1.27mm | C14267
MT3608 | U10 | Package_TO_SOT_SMD:SOT-23-6 | C84817
KF33BDT | U11 | Package_TO_SOT_SMD:TO-252-3_TabPin2
MPU6050_Breakout | U2 | TrackRay_Library:MPU6050_Breakdown
74HC595 | U3,U4,U5,U6 | Package_SO:SOIC-16_3.9x9.9mm_P1.27mm | C5947
DRV8833PWP | U7 | Package_SO:HTSSOP-16-1EP_4.4x5mm_P0.65mm_EP3.4x5mm_Mask2.46x2.31mm_ThermalVias | C50506
LM339 | U8 | Package_SO:TSSOP-14_4.4x5mm_P0.65mm | C111179
FS312 | U9 | Package_TO_SOT_SMD:SOT-23-6 | C82736
12MHz | Y1 | Crystal:Crystal_HC49-4H_Vertical

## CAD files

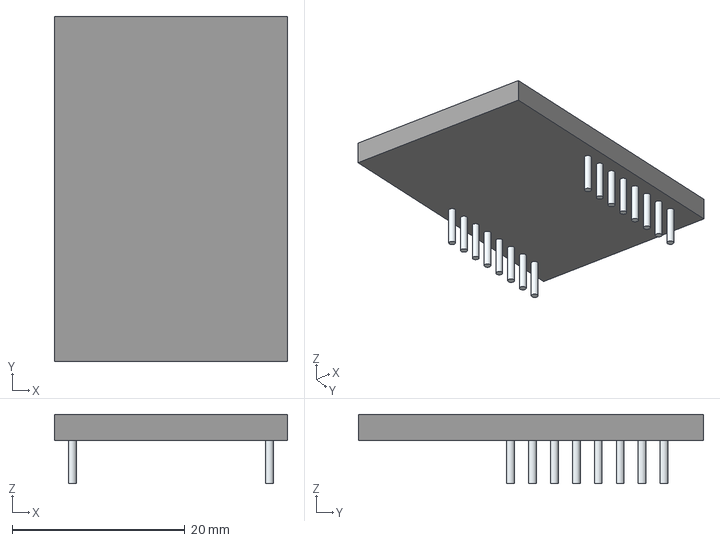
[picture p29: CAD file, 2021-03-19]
Hardware/TrackRay_H00/TrackRay_Library/3D_models/ESP32-CAM.stp
27.0 x 40.0 x 8.00 mm
Leads x 16

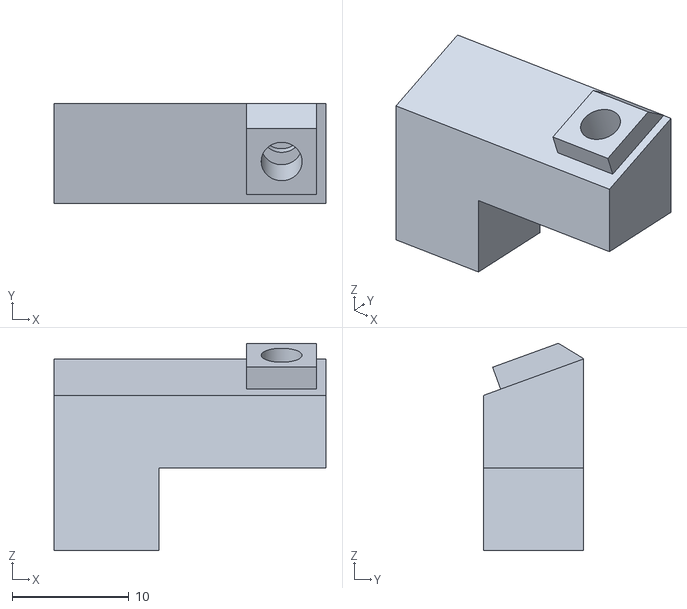
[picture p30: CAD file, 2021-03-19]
Mechanics/3D printed/1x PCB holder L.stl
23.3 x 8.60 x 17.8

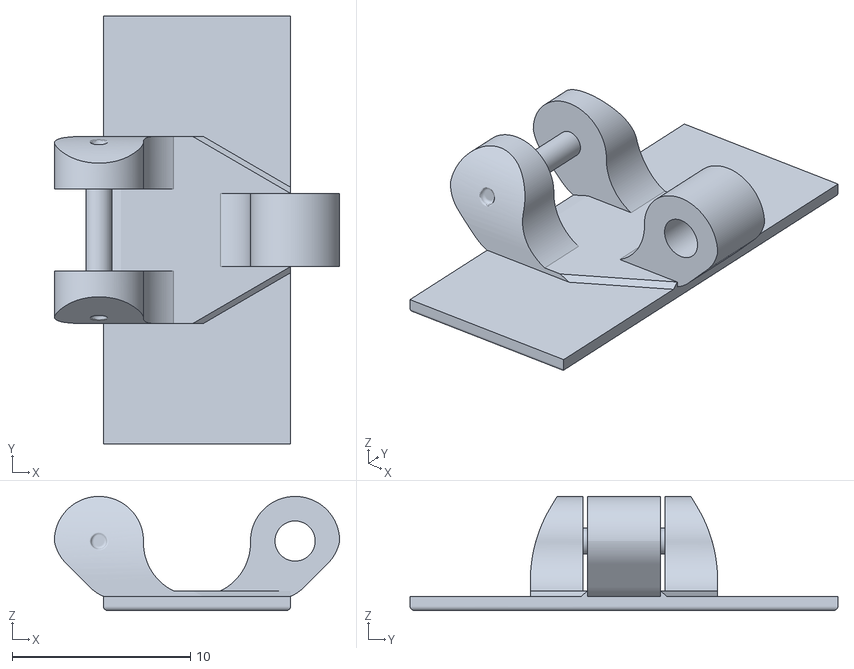
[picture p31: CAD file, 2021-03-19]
Mechanics/3D printed/Track repair kit/Repair Track segment inprinted.stl
16.0 x 24.0 x 6.40

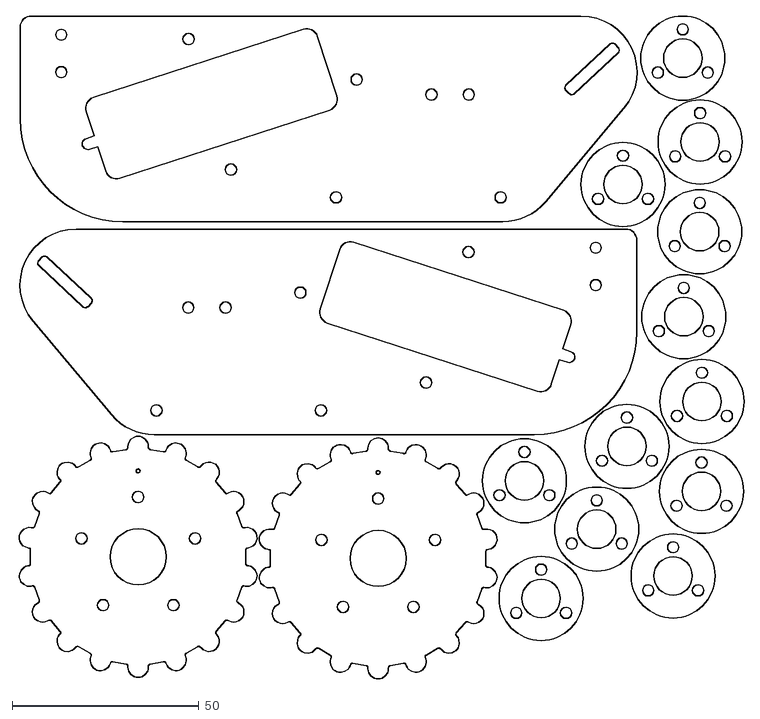
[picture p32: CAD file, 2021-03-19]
Mechanics/Lasercutter/6mm Wood.dxf
194.7 x 177.3

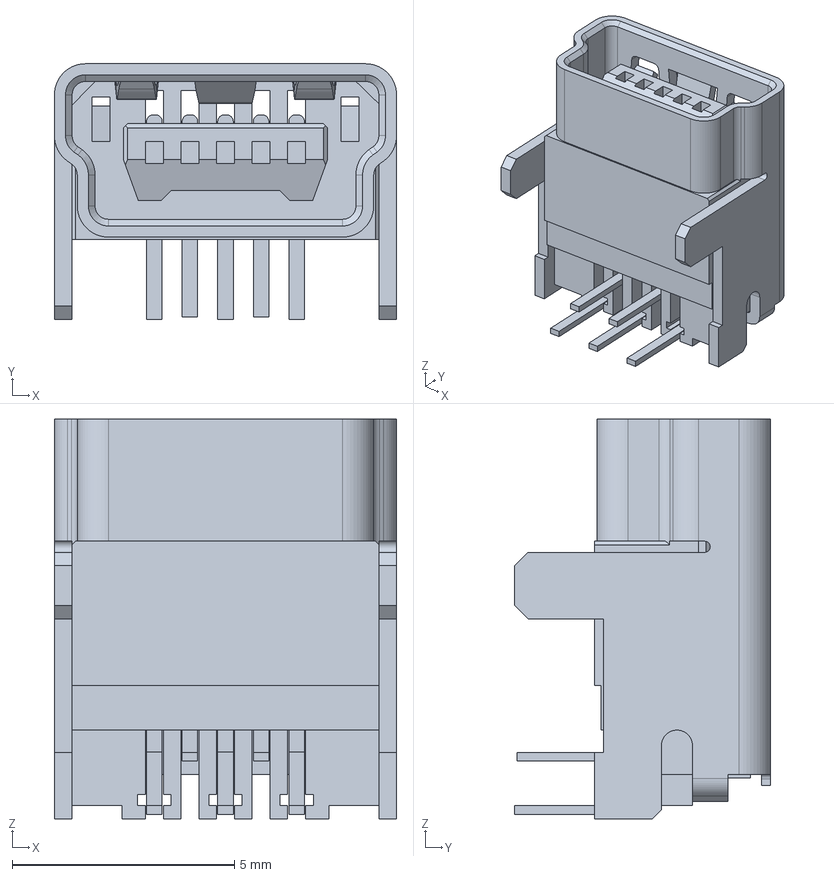
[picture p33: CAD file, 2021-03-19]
Hardware/TrackRay_H00/TrackRay_Library/3D_models/USB_MINIB.stp
7.70 x 5.75 x 9.00 mm

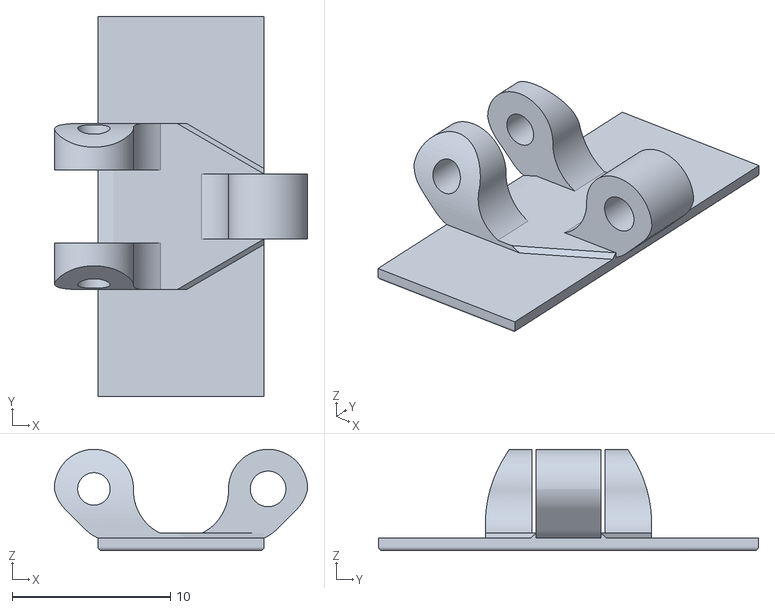
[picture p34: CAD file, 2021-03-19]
Mechanics/3D printed/Track repair kit/Repair Track Segment.stl
16.0 x 24.0 x 6.40

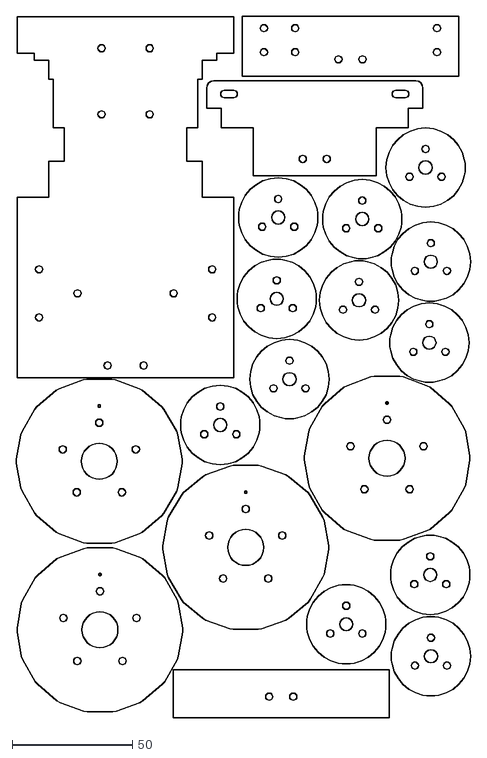
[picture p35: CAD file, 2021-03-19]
Mechanics/Lasercutter/4mm Wood.dxf
189.0 x 292.0

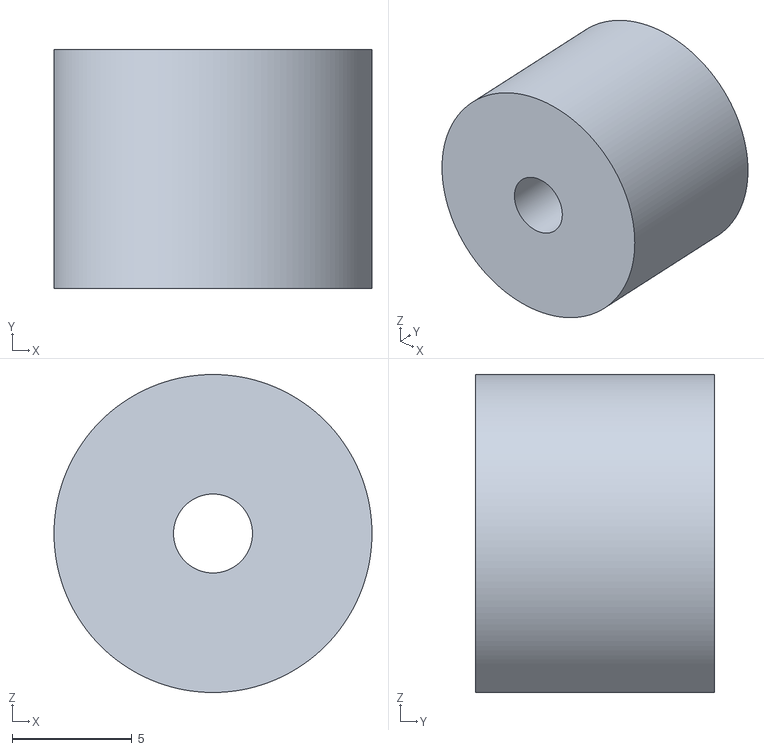
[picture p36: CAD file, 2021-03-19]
Mechanics/3D printed/2x 3DP wheel stabilizer.stl
13.3 x 10.0 x 13.3

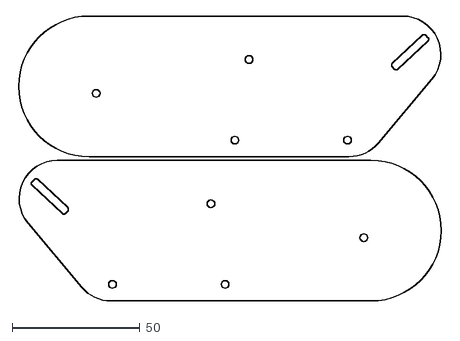
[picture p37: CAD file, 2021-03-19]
Mechanics/Lasercutter/3mm Plexi.dxf
167.0 x 111.4

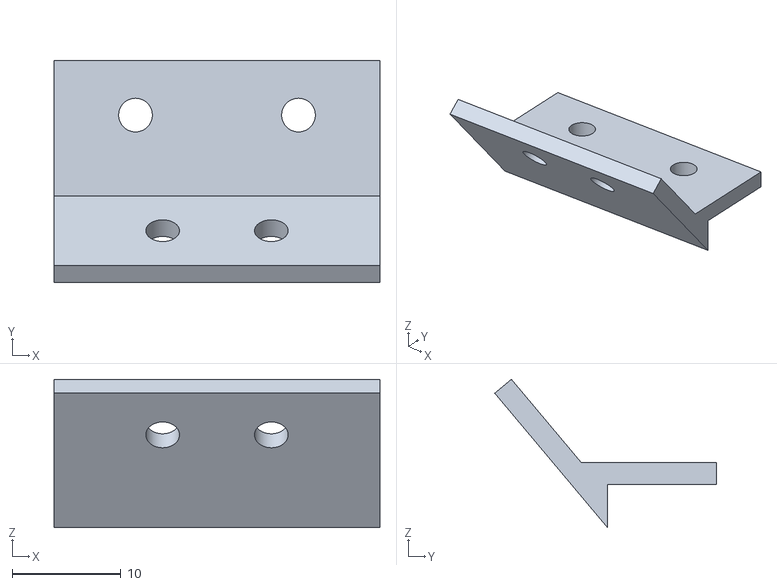
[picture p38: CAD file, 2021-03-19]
Mechanics/3D printed/1x Front Holder.stl
30.0 x 20.4 x 13.7

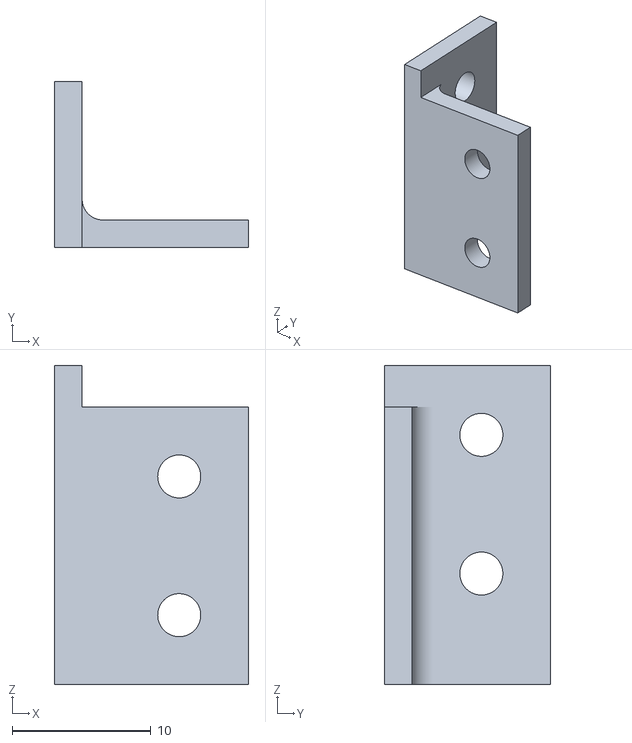
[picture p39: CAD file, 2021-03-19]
Mechanics/3D printed/1x Back Holder L.stl
14.0 x 12.0 x 23.0

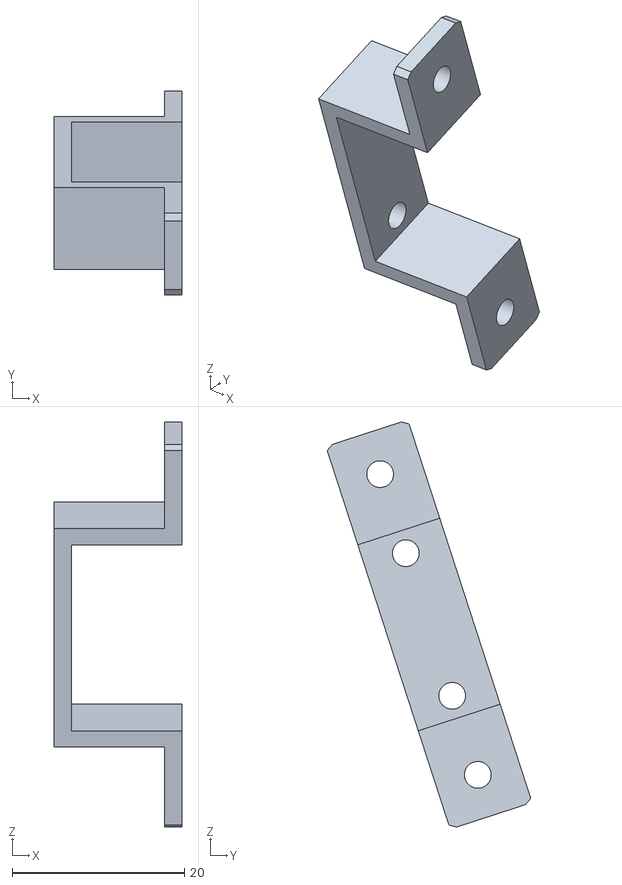
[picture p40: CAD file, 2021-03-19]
Mechanics/3D printed/2x Motor Holder.stl
14.8 x 23.6 x 47.0

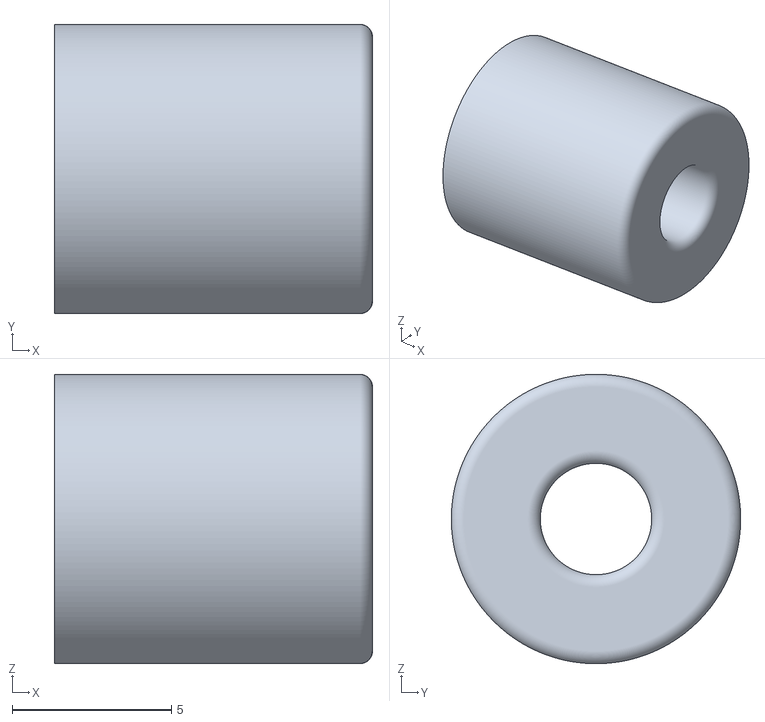
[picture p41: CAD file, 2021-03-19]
Mechanics/3D printed/6x Wheel center.stl
10.0 x 9.10 x 9.10

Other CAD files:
Mechanics/3D printed/1x PCB holder R.stl
Mechanics/3D printed/1x Back Holder R.stl
Mechanics/3D printed/1x CamHolder.stl
Mechanics/3D printed/2x Motor stabiliser.stl
Mechanics/3D printed/2x Rear wheel.stl

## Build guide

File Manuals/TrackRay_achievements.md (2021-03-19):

Toto je seznam úkolů, které tě v kombinaci s programovacím návodem naučí programovat TrackrRay.

# Obsah
* [Úkol 1 - Blikáme](#ukol1)
* [Úkol 2 - Záblesky LED](#ukol2)
* [Úkol 3 - Železniční přejezd](#ukol3)
* [Úkol 4 - Manuální blikání LED](#ukol4)
* [Úkol 5 - Stabilní stav LED](#ukol5)
* [Úkol 6 - Jízda vpřed/vzad](#ukol6)
* [Úkol 7 - Rychlost jízdy](#ukol7)
* [Úkol 8 - LED vlna](#ukol8)
* [Úkol 9 - KITT](#ukol9)
* [Úkol 10 - Ochrana náklonu](#ukol10)
* [Úkol 11 - Otočení o 90°](#ukol11)
* [Úkol 12 - Ukazatel náklonu](#ukol12)
___
## <a name = ukol1>Úkol 1 - Blikání LED</a>

### Zadání
Napiš program, který bude bude rychle blikat LED číslo 5 (v pravo nahoře na panelu).

### Parametry
Délka svícení je 200 ms. Doba zhasnutí je 200 ms. 

### Potřebné znalosti
Lekce 1

___
## <a name = ukol2>Úkol 2 - Záblesky LED</a>

### Zadání
Napiš program, který každou vteřinu krátce zableskne LED číslo 1.

### Parametry
Délka svícení je 50 ms. LED se zableskne každou vteřinu.

### Potřebné znalosti
Lekce 1

___
## <a name = ukol3>Úkol 3 - Železniční přejezd</a>

### Zadání
Napiš program, který bude blikat jako železniční přejezd.

### Parametry
Při blikání se střídají alespoň 2 různé LED. Délka svícení je volitelná.

### Potřebné znalosti
Lekce 1

___
## <a name = ukol4>Úkol 4 - Manuální blikání LED</a>

### Zadání
Napiš program, který bliká LED číslo 1 pouze při stisknutém tlačítku *SW1*.

### Parametry
Délka svícení je 200 ms. Doba zhasnutí je 200 ms. 

### Potřebné znalosti
Lekce 2

___
## <a name = ukol5>Úkol 5 - Stabilní stav LED</a>

### Zadání
Napiš program, který bude tlačítkem zapínat a vypínat LED číslo 1.

### Parametry
Po stisku tlačítka *SW1* zůstane LED 1 zapnutá. Po opětovném zmáčknutí tačítka se LED vypne.

### Potřebné znalosti
Lekce 2

___
## <a name = ukol6>Úkol 6 - Jízda vpřed/vzad</a>

### Zadání
Napiš program, který bude jezdit s TrackRay dopředu a dozadu.

### Parametry
Doba jízdy dopředu je 1 s, dozadu taky 1 s. Rychlost je libovolná nenulová.

### Potřebné znalosti
Lekce 3

___
## <a name = ukol7>Úkol 7 - Rychlost jízdy</a>

### Zadání
Napiš program, který bude tlačítkem ovládat rychlost TrackRay.

### Parametry
Při držení tlačítka *SW1* budou motory postupně zrychlovat. Po dosažení maxima začnou znovu zpomalovat.

### Potřebné znalosti
Lekce 3

___
## <a name = ukol8>Úkol 8 - LED vlna</a>

### Zadání
Napiš program, který postupně rozsvítí LEDky tak, aby vypadaly jako vlna.

### Parametry
Postupně budou rozsvíceny LED 1 až 5 v horní řadě panelu. Program běží v nekonečné smyčce.

### Potřebné znalosti
Lekce 5

___
## <a name = ukol9>Úkol 9 - KITT</a>

### Zadání
Napiš program, který bude blikat s LEDkami na motivy [Knight Rider](https://www.youtube.com/watch?v=DQkc_toDcp0).

### Parametry
Postupně budou rozsvěcovány a zhasínány LED 1 až 5 v horní řadě panelu. Program běží v nekonečné smyčce.

### Bonusové parametry
Program bude neblokující, tj. bez příkazu `delay();`.

### Potřebné znalosti
Lekce 5

___
## <a name = ukol10>Úkol 10 - Ochrana náklonu</a>

### Zadání
Napiš program, který bude hlídat náklon TrackRay.

### Parametry
Pokud velikost náklonu v alespoň jedné z os *pitch*, *roll* překoná hodnotu 20°, rozblikají se všechny LED na panelu. 

### Potřebné znalosti
Lekce 6

___
## <a name = ukol11>Úkol 11 - Otočení o 90°</a>

### Zadání
Napiš program, otočí s TrackRay o 90° v ose *yaw*.

### Parametry
Robot se bude otáčet o 90° periodicky s periodou 5 vteřin.

### Potřebné znalosti
Lekce 6

___
## <a name = ukol12>Úkol 12 - Ukazatel náklonu</a>

### Zadání
Napiš program, který bude na LED panelu TrackRay indikovat jeho orientaci v prostoru.

### Parametry
Bude svítit vždy 1 LED z panelu. Při stání na rovné podložce bude svítit prostřední LED. Při naklonění TrackRay dopředu se přesune svítící LED dopředu a obdobně do zbývajících směrů.

### Potřebné znalosti
Lekce 6

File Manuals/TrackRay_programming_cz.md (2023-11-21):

Toto je návod na programování robotického pásového vozidla TrackRay. Začněte instalací vývojového prostředí na váš PC a následně si budeme ukazovat základní pravidla programovacího jazyka C++ na příkladech.

___
# Obsah
* [Vývojové prostředí](#IDE)
* [Dálkové ovládání - kontrola robota](#kontrola)
* [Nový projekt](#novyProjekt)
* [První program](#prvniProgram)
* [Komentáře](#komentare)
* [Proměnné](#promenne)
* [Větvení](#vetveni)
* [Cyklus](#cyklus)
* [Funkce](#funkce)
* [LEDky](#ledky)
* [Tlačítko](#tlacitko)
* [Motory](#motory)
* [Sériová linka](#seriovka)
* [Výpis textu na LED panel](#panelLed)
* [Bzučák a kanón](#buzzerCannon)
* [Gyroskop](#gyroskop)
* [Připojení k WiFi](#wifi)
* [Vzdálený příkazový řádek](#remoteCmd)
* [Kamera](#kamera)
___
## <a name = IDE>Vývojové prostředí</a>

Pro programování TrackRay je použito vývojové prostředí [Visual Studio Code](https://code.visualstudio.com/download) s rozšířením PlatformIO. Pro instalaci prostředí a rozšíření můžete použít tento [návod](https://docs.platformio.org/en/latest/ide/vscode.html#installation), jehož hlavní část je na obrázku níže:

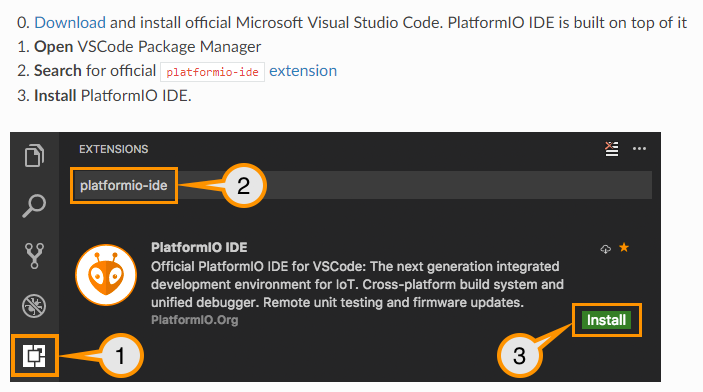
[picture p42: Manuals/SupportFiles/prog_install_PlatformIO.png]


___
## <a name = kontrola>Dálkové ovládání - kontrola robota</a>

V této části nahrajeme do TrackRay předpřipravený program pro jeho otestování. Program umožňuje dálkové ovládání TrackRay pomocí vašeho chytrého zařízení.

1. Pro naprogramování TrackRay si stáhněte [sbírku příkladů](https://github.com/vedatori/TrackRay-examples/archive/master.zip). Stáhnutý soubor *TrackRay-examples-master.zip* si rozbalte na disk svého PC na libovolnou lokaci tak, abyste ho našli. 
**Pozor:** PlatformIO má chybu - nedokáže pracovat s diakritikou v cestě k projektu. Všechny projekty musí být uloženy v cestě bez háčků a čárek!
Pokud vaše uživatelské jméno obsahuje diakritiku, tak nemůžete používat Plochu ani složku Dokumenty, ale musíte vytvořit například *C:/Vedatori/TrackRay-examples-master*.

1. Ve VS Code otevřete nabídku *File*, klikněte na *Open Folder* a zvolte složku *RemoteControl* z dříve rozbalené sbírky příkladů *TrackRay-examples-master*.

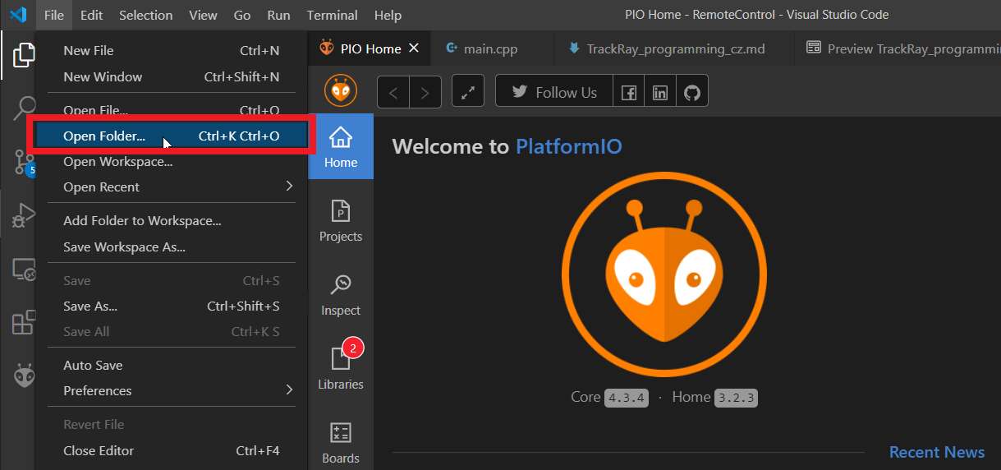
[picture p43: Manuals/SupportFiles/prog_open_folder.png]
    
1. Otevřete soubor *main.cpp* který je v cestě *RemoteControl/src/main.cpp*.

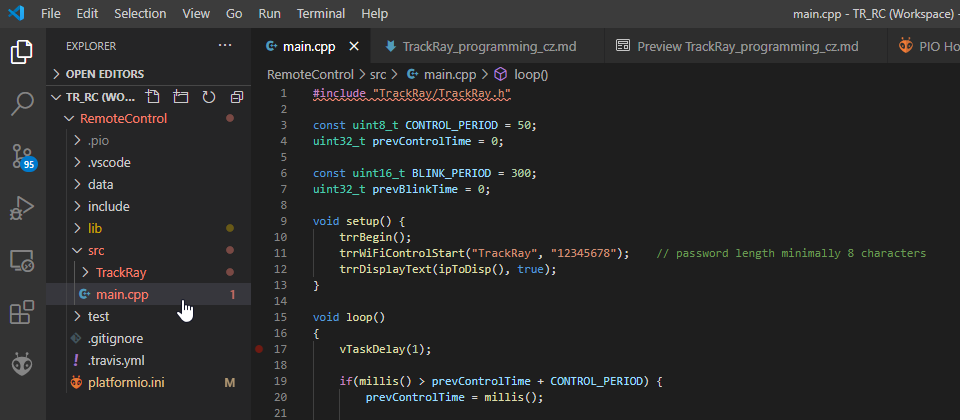
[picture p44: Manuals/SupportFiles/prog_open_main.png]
    
1. Na řádku 11 upravte název robota "TrackRay" tak, aby byl poznatelný, např. ve formátu "TrackRay_jmeno". Můžete upravit i heslo, ale pozor, aby mělo alespoň 8 znaků.

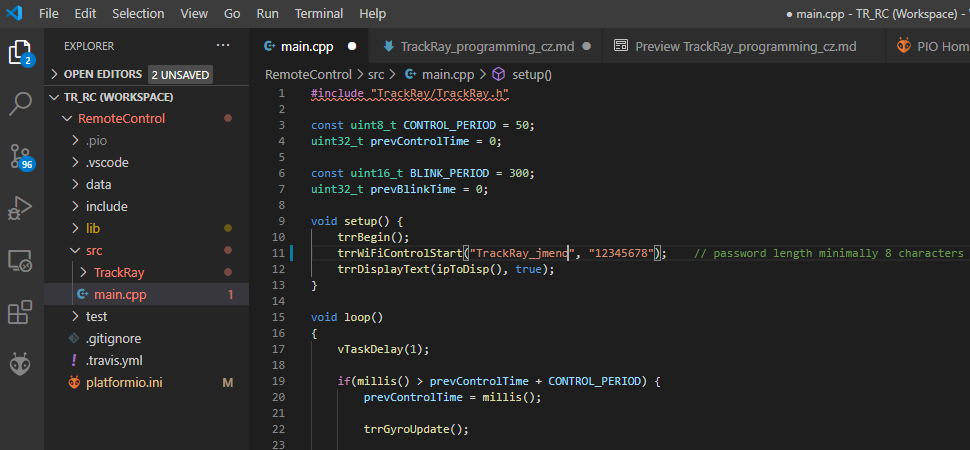
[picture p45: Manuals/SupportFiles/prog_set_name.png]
    
1. Po otevření projektu bude VS Code chvíli pracovat. Pokud ještě pracuje, počkejte, dokud text na dolní liště nezmizí.
   
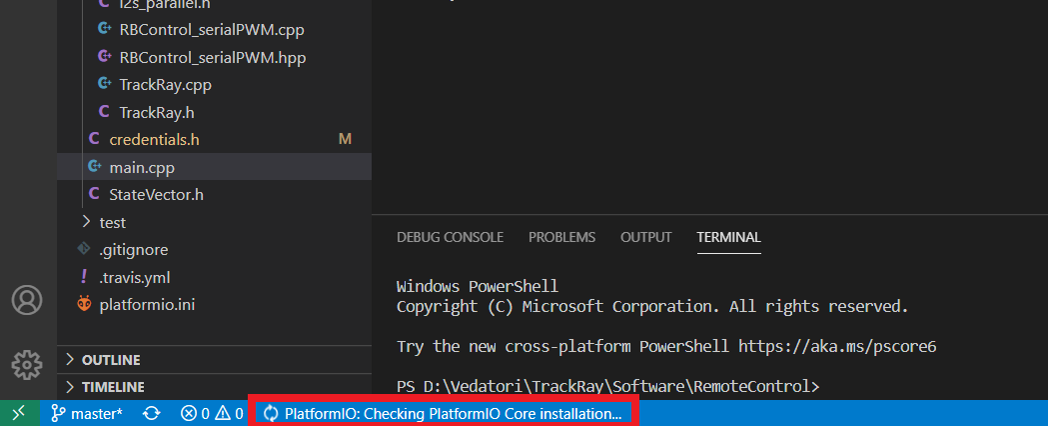
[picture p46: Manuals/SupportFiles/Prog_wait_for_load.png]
    
1. Připojte TrackRay pomocí USB Mini B kabelu k PC.
1. V dolní liště PlatformIO stiskněte šipku a tím nahrejte program do TrackRay.

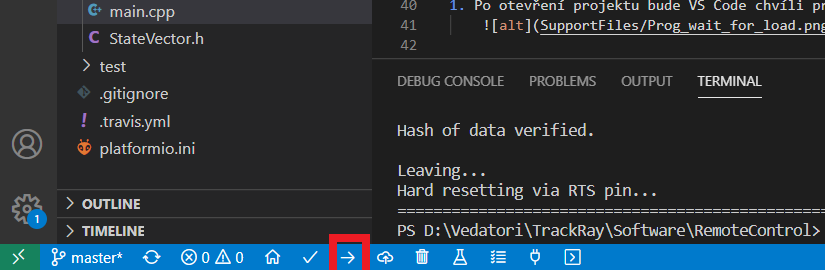
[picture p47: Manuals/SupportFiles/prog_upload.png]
    
1. Počkejte, až se dokončí nahrávání a zobrazí v dolním terminálu *SUCCESS*.

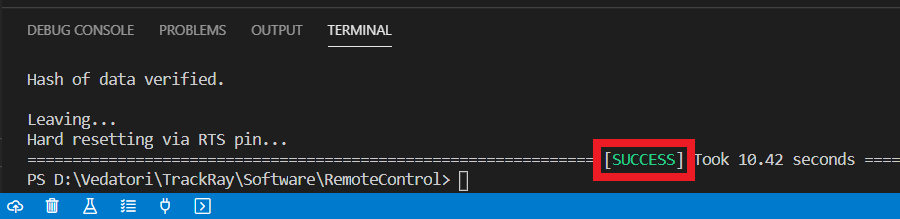
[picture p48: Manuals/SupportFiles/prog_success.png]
    
1. V dolní liště PlatformIO stiskněte tlačítko úplně v pravo a tím spusťe PlatformIO terminál.

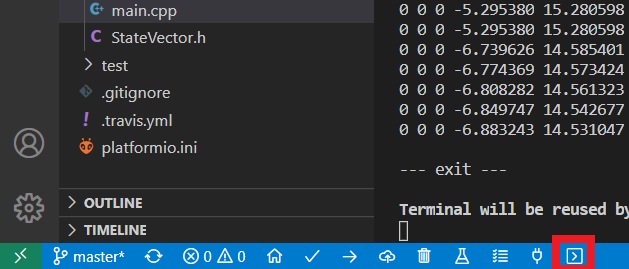
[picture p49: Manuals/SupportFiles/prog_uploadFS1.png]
    
1. Do nově otevřeného termínálu v dolní částí VS Code zadejte příkaz 'pio run -t uploadfs' a stiskněte *ENTER*.

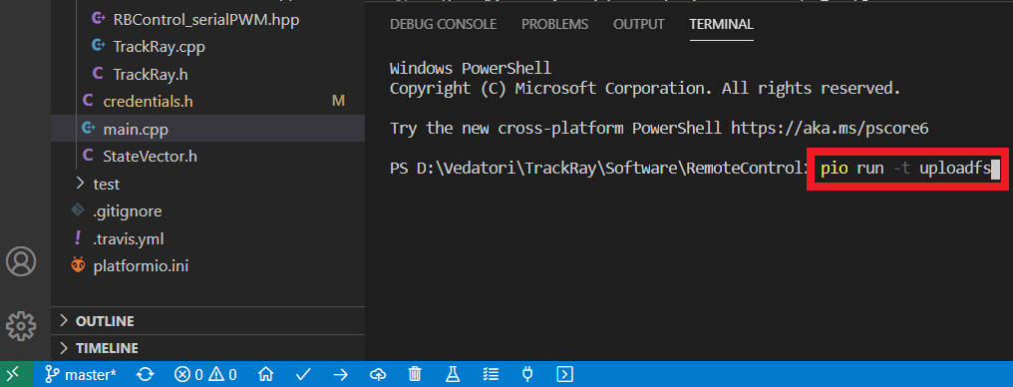
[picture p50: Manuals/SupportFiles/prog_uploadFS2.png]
    
1. Počkejte, až se dokončí nahrávání a zobrazí v dolním terminálu *SUCCESS*.

    
1. Nyní je robot plně naprogramován. Pro ovládání na svém chytrém zařízení vyhledejte WiFi síť s názvem *TrackRay* nebo s vámi zvoleným jménem a heslem. Podle typu vašeho zařízení vám pak může vyskočit tlačítko na přihlášení do sítě "Sign in" jako např. pro Android:

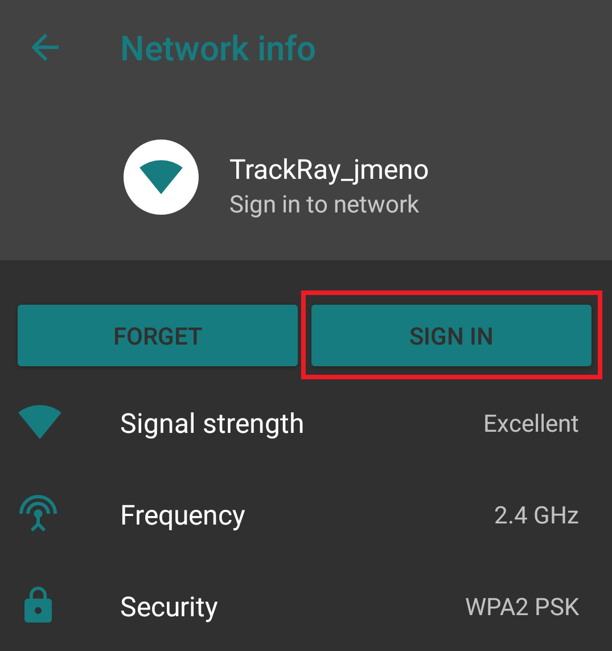
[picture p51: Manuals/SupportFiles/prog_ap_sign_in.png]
    
1. Pokud se žádná výzva k přihlášení neobjeví, zadejte do webového prohlížeče adresu *192.168.4.1* nebo jakoukoli jinou ve tvaru *www.neco.cz*. Načte se hlavní stránka pro ovládání TrackRay. Joystickem ovládejte pohyb. Na počítači můžeš použít šipky. Do políčka *Command entry* zadávejte speciální příkazy.

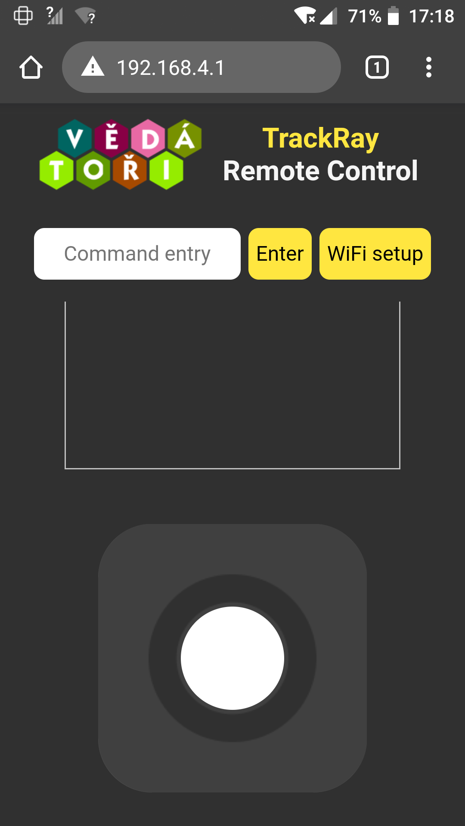
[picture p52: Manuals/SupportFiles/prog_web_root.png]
    
1. Pro přihlášení TrackRay k externí WiFi síti klikněte na tlačítko *WiFi setup*. Na následující stránce zadejte přihlašovací údaje od externí WiFi a potvrďte přihlášení.

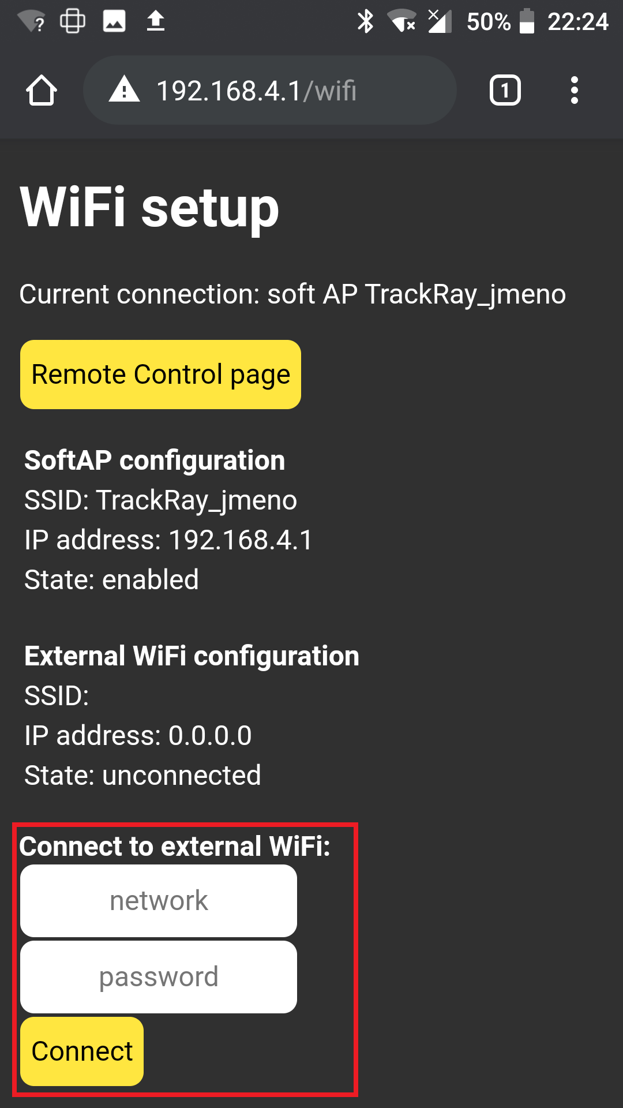
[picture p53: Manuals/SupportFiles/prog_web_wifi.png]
    
1. Pokud přihlášení proběhne úspěšně, objeví se potvrzení *connected* a přidělená IP adresa. Tato síť bude vyhledána i po restartu. Připojte se svým chytrým zařízením také na externí WiFi a zadejte do prohlížeče přidělenou IP adresu. V tomto případě *192.168.1.152*. Tato adresa bude po restartu zobrazena i na panelu TrackRay. 

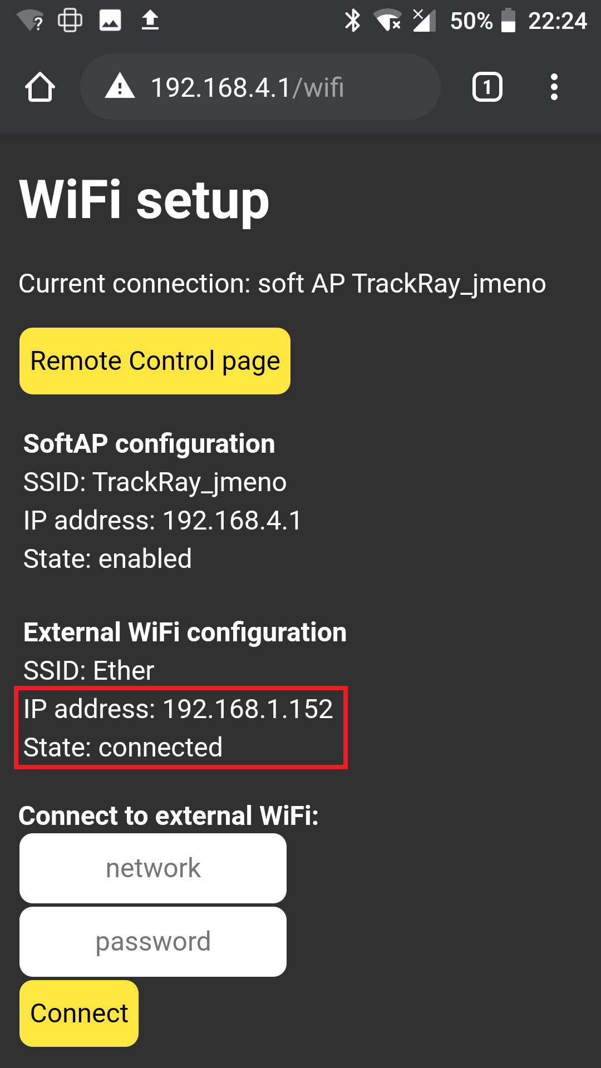
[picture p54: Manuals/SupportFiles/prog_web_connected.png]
    
1. Načte se opět hlavní stránka ovládání TrackRay. Tímto je vypnuta interní WiFi *TrackRay_jmeno*. Pro její opětovné zapnutí přejděte do nastavení WiFi a klikněte na tlačítko *Enable AP* nebo restartujte TrackRay.

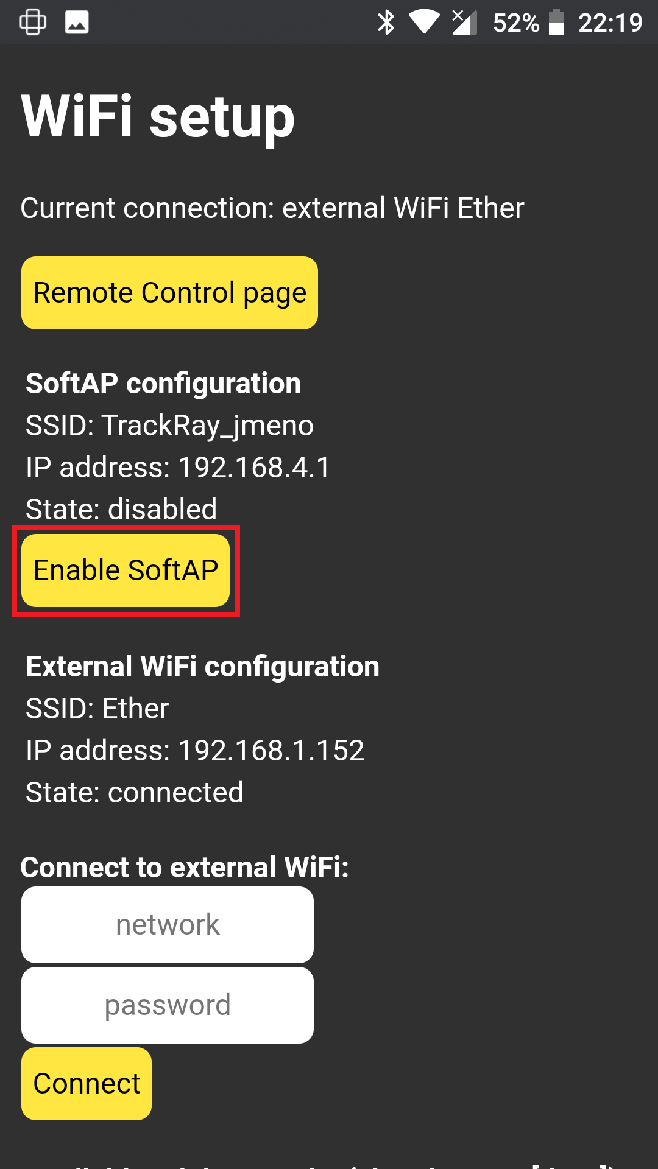
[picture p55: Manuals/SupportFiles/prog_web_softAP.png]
    
1. Pro ovládání TrackRay textovými příkazy z dema *RemoteControl* můžete používat následující příkazy. Příkazy nejsou citlivé na velikost použitých písmen.
    * `flash on` - Zapne přední reflektor na plný výkon. Pozor, LED je poměrně silná. Nedoporučejeme používat příliš dlouho. Může dojít k *utavení* plastového držáku zrcadla a čočky.
    * `flash half` - Zapne přední reflektor na poloviční výkon
    * `flash off` - Vypne přední reflektor
    * `flash 49` - Zapne přední reflektor na 49% výkon. Můžeš poučít libovolné celé číslo <0, 100>.
    * `cam on` - Zapne kamerový přenos z TrackRay.
    * `cam off` - Vypne kamerový přenos.
    * `shoot` - Vystřelí čili zapne motor děla na 1 vteřinu.
    * `beep` - Zapne buzzer na 0,5 vteřiny.

___
## <a name = novyProjekt>Nový projekt</a>

Vytvoříme nový projekt a nahrajeme program do TrackRay.

1. Vytvoř si na disku svého PC složku pro tvé budoucí programy, například *C:/Vedatori/TrackRay-moje-programy*.
1. Do této nové složky překopíruj složku *demo_project* ze sbírky příkladů *TrackRay-examples-master*. Tato složka *demo_project* bude sloužit jako šablona tvých budoucích programů pro TrackRay. 
1. Překopírovanou složku *demo_project* přejmenuj na *01_prvni_program*.
1. Ve VS Code otevři složku *01_prvni_program* pomocí *File*->*Open folder*.
1. Připojte TrackRay pomocí USB Mini B kabelu k PC.
1. V dolní liště PlatformIO stiskněte šipku a tím nahrejte program do TrackRay.
    
1. Počkejte až se dokončí nahrávání a zobrazí v dolním terminálu *SUCCESS*.
    

___
## <a name = prvniProgram>První program</a>
Otevři si soubor *main.cpp*. Programovat robota budeme hlavně v tomto souboru. Nahraď celý jeho obsah následujícím minimálním kódem:
```
#include "TrackRay/TrackRay.h"

void setup() {
    trrBegin();
    trrSetLedDigital(D1, true);
}

void loop() {
    
}
```

1. `#include "TrackRay/TrackRay.h"` - Příkaz *#include* značí co všechno můžeš ve svém programu používat. Nyní nám bude stačit přidání knihovny *TrackRay.h*.
1. `void setup() {}` - To, co vidíš zde, je funkce. Funkce jsou kusy kódu, které můžeš opakovaně spustit tak, že zavoláš jméno. Kód každé funkce je ohraničen složenými závorkami { a }, a uvnitř také odsazen. Tato funkce se jmenuje *setup* a je spuštěna jedenkrát po zapnutí TrackRay.
1. `trrBegin();`
1. `void loop()` - Tato funkce se jmenuje *loop* a je spouštěna stále pořád dokola dokud je TrackRay zapnutý.

### Tvůj kód
Nyní napíšeš svůj první vlastní program na TrackRay. Na příslušné místo v tvém kódu přepiš řádek `trrSetLedDigital(D1, true);`. Tento řádek patří na konec funkce *setup*, tedy před uzavírací závorku }.

Všimni si, že při psaní ti VS Code napovídá. Stačí napsat *trr* a uvidíš všechny metody, které můžeš používat na řízení TrackRay. Pokud se tak nestane, nabídku vyvoláš stisknutím *Ctrl + Space*.

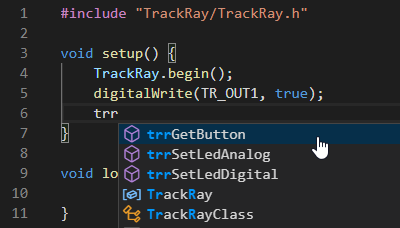
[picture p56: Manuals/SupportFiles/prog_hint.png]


Funkce *trrSetLedDigital* slouží k zapínání a vypínání LED světel na TrackRay. Jedná se o volání funkce s parametry v kulatých závorkách ( a ).
1. parametr udává kterou LED chceme ovládat. V tomto případě budeme ovládat LED úplně vlevo nahoře, která se jmenuje *D1*.
1. parametr udává jestli má LED od nyní svítit (`true`) nebo nesvítit (`false`).

Nahraj program do TrackRay a počkej až se první LED rozsvítí. Gratulujeme, toto byl tvůj první vlastní program pro TrackRay :-)

___
## <a name = komentare>Komentáře</a>

Do svého kódu je někdy vhodné psát komentáře. Komentáře jsou kusy textu, které jsou viditelné pro programátora, čili tebe, ale TracRay si jich nevšímá. Jsou vhodné zejména v místech, kdy ze samotného funkčního kódu není zřejmé co dělá a k čemu slouží.

V jazyce C++ máme 2 typy komentářů:
1. Jenořádkový komentář je uvozen dvojitým lomítkem `//`. Celý zbytek řádku za dvojitým lomítkem je považován za komentář.
1. Víceřádkový komentář je uvozen lomítkem a hvězdičkou `/*`. Ukončen je hvězdičkou a lomítkem `*/`. Veškerý text mezi je považován za komentář. Začátek a konec mohou být na různých řádcích.

Příklad: Tento program nerozsvítí LEDku.
```
#include "TrackRay/TrackRay.h"

void setup() {
    trrBegin();
    // trrSetLedDigital(D1, true);
}

void loop() {
    
}
```

___
## <a name = promenne>Proměnné</a>

### Motivace
Při psaní programů brzy dojdete k tomu, že potřebujete aby si program něco *zapamatoval*. Může se jednat o výsledek matematicé rovnice, počítadlo kroků, uchování měřené hodnoty a tak dále. K tomuto účelu se v programech používají **proměnné**. Proměnné si můžeme představovat jako šuplíky s textovými popisky na sobě. Do šuplíku můžeme *vložit* nějakou informaci a někdy později ji opět vytáhnout. Popisek šuplíku zde představuje název proměnné.

### Vytvoření proměnné
Proměnnou vytvoříme následujícím příkazem:
```
typ_promenne nazev_promenne = hodnota;
```
`typ_promenne` udává jaký typ informace budeme do proměnné ukládat. Říkáme mu také *datový typ proměnné*. Může to být číslo, text atd.

`nazev_promenne` udává název proměnné, pomocí kterého dokážeme od sebe jednotlivé proměnné odlišit. Proto musí mít každá proměnná svůj jedinečný název. Snaž se pojménovávat proměnné výstižně, tedy např. *rychlost* je mnohem lepší než *prom*. V názvu proměnné můžeš používat znaky anglické abecedy, tj. bez diakritiky, velká a malá písmena, čísla a speciální znaky jako podrtžítko `_`. Podtžítkem můžeme oddělovat slova v názvu jedné proměnné.

`=` je operátor sloužící k přiřazení (vložení) určité hodnoty do proměnné.

`;` čili středník slouží k oddělování příkazů a píšeme ho vždy na konec příkazu. Na české klávesnici se nachází pod klávesou *ESC*.

### Základní datové typy proměnných
* `int` označuje proměnnou pro ukládání celých čísel, například `3`.
* `float` označuje proměnnou pro ukládání desetinných čísel, například `3.14`.
* `char` označuje jeden textový znak -> znak se udává v apostrofech, například `'c'` označuje znak *c*.
* `bool` označuje pravdivostní hodnotu -> *true* pro pravdu a *false* pro nepravdu.
* `std::string` označuje řetězec textových znaků -> řetězec se ohraničuje uvozovkami, například `"Ahoj svete"`.

### Operace s proměnnými

Operace *přiřazení* slouží k uložení dané hodnoty do proměnné. Hodnota, která je napravo od rovnítka `=` je uložena do proměnné uvedené nalevo od `=`: 
```
nazev_promenne = hodnota;
```

Číselné proměnné můžeme sčítat (+), odečítat (-), násobit (*) a dělit (/). 

Příklad:
```
#include "TrackRay/TrackRay.h"

void setup() {
    trrBegin();
    int cele_cislo = 0;
    cele_cislo = cele_cislo + 10;   // Zvýšíme hodnotu v proměnné o 10
    cele_cislo += 10;   // Zkrácený zápis toho stejného
    // Nyní je v proměnné cele_cislo uloženo 20
}

void loop() {
    
}
```

Zde jsou uvedeny příklady vytvoření proměnných zmíněných datových typů a uložení hodnoty do nich.
```
// proměnná pro celá čísla se jménem cele_cislo, ve které je hodnota 0
int cele_cislo = 0; 

// promenna pro desetinne cislo ve které je hodnota 3.14
float desetinne_cislo = 3.14; 

// proměnná znak, do které jsme uložili znak 'a'
char znak = 'a';

// proměnná otevreno, do které jsme uložili hodnotu pravda (true)
bool otevreno = true; 

// proměnná pro textový řetězec s hodnotou "nejaky text"
std::string text = "nejaky text";
```
___
## <a name = vetveni>Větvení</a>

### Motivace
Při programování brzo zjistíš, že potřebuješ, aby se tvůj program choval různě v různých situacích. Jinými slovy aby prováděl určité úseky kódu pouze za splnění daných podmínek. Tomuto chování říkáme *větvení* a umožňuje programu provádět *rozhodnutí*.

### Konstrukce `if`
`if` je základní podmíněný příkaz. Základem této konstrukce je *podmínka*, která se uvádí za slovo if do kulatých závorek. Podmínka může být proměnná nebo logický výraz.
```
if(podminka) {
    ...kód který se provede, pokud je podmínka splněna (true)...
}
```
U `if` konstrukce docházi k vyhodnocení podmínky, tj. zjistí se, zda je podmínka pravdivá (`true`) nebo nepravdivá ((`false(`). Pokud je pravdivá, provede se kód, který je za `if` uveden ve složených závorkách `{...kód...}`. V opačném případě program pokračuje až za `if`.

### Konstrukce `else`
Může existovat jen v případě, kdy před ní byl vyvořený `if`. Úkolem `else` je provést kód v něm napsaný jen v případě, že předchozí `if` nebyl splněn.
```
if(podminka) {
    ...kód který se provede, pokud je podmínka splněna (true)...
}
else {
    ...kód který se provede, pokud není podmínka splněna (false)...
}
```

### Konstrukce `else if`
Pokud chceme postihnout více možných příapadů než dva dříve zmíněné (`true` a `false`), použijeme konstrukci `else if`.
```
if(podminka_1) {
    ...kód který se provede, pokud je podmínka 1 splněna (true)...
}
else if(podminka_2) {
    ...kód který se provede, pokud je podmínka 2 splněna (true)...
}
else {
    ...kód který se provede, pokud není podmínka 1 ani 2 splněna (false)...
}
```

Poznámka: V jednotlivých konstrukcích větvení je možné libovolně vnořovat další konstrukce větvení.

### Podmínka
Podmínka dotazovaná při větvení určuje zda se bude daný úsek kódu provádět. K tomu je porovnávána s logickými hodnotami `true` a `false`. Tato hodnota může být uložena v pravdivostní proměnné typu `bool`:
```
bool podminka = true;
if(podminka) {
    ...kód, který je vykonán, protože podmínka je pravdivá...
}
```

K vytvoření podmínky z číselné hodnoty budeme používat tzv. *relační operátory*:
* `==` označuje porovnávání, takže 1 == 1 označuje, že se 1 rovná 1
* `!=` vykřičník před rovnítkem označuje opak, tudíž tento operátor značí nerovnost, tedy 1 != 2 označuje, že se 1 nerovná 2
* `<` menší než
* `>` větší než
* `<=` menší nebo rovno než
* `>=` větší nebo rovno než
Výsledek výrazu s relačními operátory nabývá hodnotu pravda `true` nebo nepravda `false`.
Příklad relačního operátoru:
```
int cele_cislo = 3;
if(cele_cislo < 5) {
    if (cele_cislo > -5) {
        cele_cislo = 0;
    }
}
// V proměnné cele_cislo je uložena hodnota 0
```

### Propojování podmínek
Podmínky je možné propojovat do jedné složitější pomocí logických operátorů. Jsou jimi
* `&&` (logické *A*) říká nám, že musí platit obě podmínky, aby byla podmínka splněna, jinak je nesplněna
* `||` (logické *NEBO*) říká nám, že musí platit alespoň jedna podmínka z nich, aby byla podmínka splněna, jinak je nesplněna
Ukázka: Následující program funguje stejně jako předchozí, používá ovšem využívá logické operátory.
```
int cele_cislo = 3;
if(cele_cislo < 5 && cele_cislo > -5) {
    cele_cislo = 0;
}
// V proměnné cele_cislo je uložena hodnota 0
```
___
## <a name = cyklus>Cyklus</a>

### Motivace
Při programování se nám často stane, že potřebujeme některé úkony vykonat vícekrát. Případně vykonat velké množství podobných úkonů. K tomuto budeme používat *cykly*, které nám umožní opakovaně vykonávat úseky kódu.

Pro jedno bliknutí LEDkou poslouží tento program:
```
#include "TrackRay/TrackRay.h"

void setup() {
    trrBegin();
    trrSetLedDigital(D1, true);
    delay(500);
    trrSetLedDigital(D1, false);
    delay(500);
}

void loop() {
    
}
```
V tomto programu používáme příkaz *delay()* pro čekání na místu v kódu o určitý čas. Tento čas čekání je určen v milisekundách (1000 ms = 1s).

Pro 3 bliknutí LEDkou poslouží tento program, ve kterém jsme pouze zopakovali příkazy z minulého:
```
#include "TrackRay/TrackRay.h"

void setup() {
    trrBegin();
    trrSetLedDigital(D1, true);
    delay(500);
    trrSetLedDigital(D1, false);
    delay(500);

    trrSetLedDigital(D1, true);
    delay(500);
    trrSetLedDigital(D1, false);
    delay(500);

    trrSetLedDigital(D1, true);
    delay(500);
    trrSetLedDigital(D1, false);
    delay(500);
}

void loop() {
    
}
```

Ale co kdybychom chtěli bliknout 1000 krát? Kód by nás přerostl. Cykly nám pomohou tento problém vyřešit. 

### Cyklus `while`
Cyklus `while` použijeme v případě, kdy předem nevíme, kolikrát chceme kód opakovat. Cyklus `while` se opakuje dokud je splněna jeho podmínka (`true`).
```
while(podminka){
    ...Co se ma provest pri kazdem opakovani...
}
```

V následném kódu budeme blikat LEDkou dokud bude TrackRay zapnutý:
```
while(true){
    trrSetLedDigital(D1, true);
    delay(500);
    trrSetLedDigital(D1, false);
    delay(500);
}
```

### Cyklus `for`
Cyklus `for` použijeme v případě, kdy dopředu známe, kolikrát chceme kód opakovat. Cyklus `for` má následující formu:
```
for(vytvoreni_promenne; podminka; operace){
    ...Co se ma provest pri kazdem opakovani...
}
```

Oproti cyklu while je zde podmínková část složitější, než v případě while cyklu. Skládá se ze 3 částí:
* Vytvoř proměnnou, kterou využiješ v podmínce
* Zadej podmínku, která bude udávat, do kdy máme kód opakovat
* Uprav hodnotu proměnné, pokud je podmínka splněna

Následující program ukazuje, jak bliknout 10x s LED číslo 1 pomocí cyklus `for`.
```
for(int pocet_bliku = 0; pocet_bliku < 10; pocet_bliku++){
    trrSetLedDigital(1, true);
    delay(500);
    trrSetLedDigital(1, false);
    delay(500);
}
```
Vytvořili jsme proměnnou `pocet_bliku`, která obsahuje celé číslo 0. Dokud je tato proměnná menší než 10, tak se k ní přičte hodnota 1 a provede se kód.

<!---
___
## <a name = funkce>Funkce</a>
**TODO**
-->

___
## <a name = ledky>LEDky</a>
V této kapitole konečně rozsvítíme LEDky na panelu Trackray.

Pro ovládání LED na TrackRay můžete použít následující funkce:
* `trrSetLedDigital()` - rozsvícení a zhasnutí jedné LED
* `trrSetLedAnalog()` - nastavení jasu jedné LED v rozsahu 0 (nesvítí) až 100 (plně svítí)
* `trrSetLedAllDigital()` - rozsvícení a zhasnutí všech LED na panelu
* `trrSetLedAllAnalog()` - nastavení jasu všech LED na panelu v rozsahu 0 (nesvítí) až 100 (plně svítí)
* `trrSetFlashLightDigital(const bool state)` - rozsvícení a zhasnutí LED reflektoru
* `void trrSetFlashLightAnalog(const int8_t value))` - nastavení jasu LED reflektoru

Pro rozsvícení LED číslo 1 vlevo nahoře použijeme příkaz:
```
trrSetLedDigital(1, true);
```
Stejně tak můžeme pro rozsvícení použít příkaz:
```
trrSetLedAnalog(1, 100);
```
Obdobným způsobem ovládáme zbylé LEDky.
___
## <a name = tlacitko>Tlačítko</a>
Nejjednodušším způsobem, jak můžete TrackRay ovládat je pomocí tlačítka **SW1**, které najdete v pravém horním rohu desky elektroniky. Pro zjištění jestli je tlačítko zmáčknuto budeme používat příkaz `trrReadButton` v náslející konstrukci.
```
bool tlacitko_zmacknuto = trrReadButton();
```
Zde je vytvořenap roměnná `tlacitko_zmacknuto` a následně do ní uložen stav tlačítka voláním příkazu `trrReadButton`, který nabývá pravdivostní hodnoty `true` nebo `false`.

Příklad: Tento program rozsvítí LED 1 na panelu při stisku tlačítka SW1.
```
#include "TrackRay/TrackRay.h"

void setup() {
    trrBegin();
}

void loop() {
    if(trrReadButton()) {
        trrSetLedDigital(1, true);
    }
    else {
        trrSetLedDigital(1, false);
    }
}
```

Protože příkaz `trrReadButton` nabývá pravdivostní hodnoty `true` nebo `false`, můžeme předchozí program zapsat úsporněji, ale funkčně stejně jako:
```
#include "TrackRay/TrackRay.h"

void setup() {
    trrBegin();
}

void loop() {
    trrSetLedDigital(1, trrReadButton());
}
```
___
## <a name = motory>Motory</a>
Nyní konečně pořádně oživíme TrackRay a začneme s ním pohybovat.

Pro řízení motorů můžete použít následující příkazy:
* `trrMotorsSetSpeed()` - nastaví rychlost obou motorů podle 2 zadaných číselných parametrů v rozshahu -100 až 100.
* `trrMotorsSetSpeedLeft()` - nastaví rychlost levého motoru podle zadaného číselného parametru v rozshahu -100 až 100.
* `trrMotorsSetSpeedRight()` - nastaví rychlost pravého motoru podle zadaného číselného parametru v rozshahu -100 až 100.

Příklad: Následujícím příkazem rozjedeme TrackRay na poloviční rychlost dopředu:
```
trrMotorsSetSpeed(50, 50);
```
Úplně stejně bude fungovat i následující dvojice příkazů:
```
trrMotorsSetSpeedLeft(50);
trrMotorsSetSpeedRight(50);
```

### Kanón
Motor kanónu budeme ovládat pomocí příkazu `trrCanonSetSpeed()`. Rychlost motoru bude nastavena podle zadaného číselného parametru v rozshahu 0 až 100.

Pro spuštění motoru kanónu na plno použijeme příkaz:
```
trrCanonSetSpeed(100);
```

___
## <a name = seriovka>Sériová linka</a>

### Motivace
Při programování robotů se často stane, že potřebujete s programem v robotovi komunikovat. Například když se snažíš odhalit chybu, vypisovat hodnotu senzorů nebo informovat uživatele o ději v programu. Pro tento účel nám poslouží sériová linka.

### Program pro výpis textu na sériové lince
Pro výpis textu na sériové lince budeme používat příkaz `printf`. Abychom na sériové lince jedenkrát vypsali text *Hello World!*, použijeme následující program:
```
#include "TrackRay/TrackRay.h"

void setup() {
    trrBegin();
    printf("Hello World!\n");
}

void loop() {

}
```
Okolo textu, který chceme vypsat je třeba vložit dvojité uvozovky `"text"`. Řetězec `/n` označuje znak pro odřádkování, čili obdoba tlačítku *ENTER* v textových editorech. 

### Spuštění sériové linky
1. Po nahrání programu do TrackRay necháme TrackRay připojený USB kabelem k PC.
1. Pomocí tlačítka v levé dolní liště PlatformIO ve tvaru zásuvky spustíme sériovou linku.

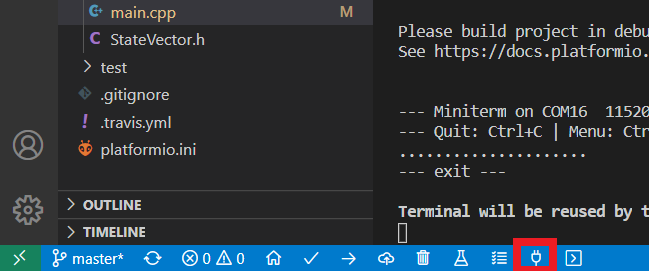
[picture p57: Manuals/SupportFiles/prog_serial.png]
    
1. Se spuštěnou sériovou linkou je třeba resetovat TrackRay, aby mohl jednou po startu vypsat žádaný text. Provedeme to stisknutím tlačítka RESET ze spodní strany modulu *ESP-CAM*:

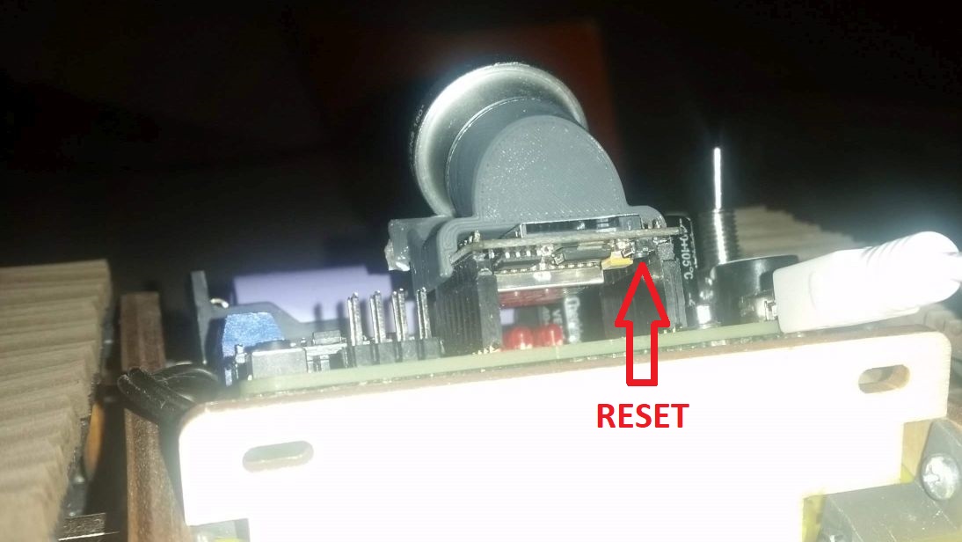
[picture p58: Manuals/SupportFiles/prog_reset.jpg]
    
1. Na otevřené sériové lince v dolní částí okna VS Code najedte zadatý textový řetězec *Hellp World!*:
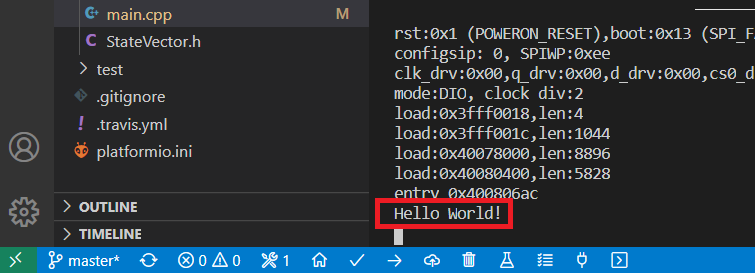
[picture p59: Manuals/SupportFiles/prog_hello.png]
    

### Výpis hodnot proměnných
Často potřebujeme vypsat i hodnotu některé z našich proměnných. V tomto případě můžeme použít takzvaná formátovací direktiva. V textu začínají znakem `%`:
* %d - (decimal) označuje celé číslo
* %f - (float) značí desetinné číslo
* %c - (char) označuje znak
* %s - (string) značí řetězec 

Pro úpravu formátu vypisovaných proměnných máme mnoho dalších možností, které nalezneš například na [Wiki](https://cs.wikipedia.org/wiki/Printf#Form%C3%A1tovac%C3%AD_%C5%99et%C4%9Bzec). Pro výpis celočíselné proměnné `cele_cislo` do sériové linky použijeme následující příkaz:
```
printf("%d\n", cele_cislo);
```

Příklad: Pro opakovaný výpis času od startu TrackRay použijeme následující program. Hodnota času je uvedena v milisekundách:
```
#include "TrackRay/TrackRay.h"

void setup() {
    trrBegin();
}

void loop() {
    printf("%d\n", millis());
    delay(500);
}
```
Funkce `millis()` nám vrací počet uplynulých milisekund od startu programu jako celé číslo.

___
## <a name = panelLed>Výpis textu na LED panel</a>
Pro výpis textu na LED panel TrackRay slouží následující funkce:
* `trrDisplayText(String text, bool sweep = true)` - postupně vypíše zadaný *text* v datovém typu *String*. Druhý pravdivostní parametr *sweep* je nepovinný a určuje, zda bude text odjíždět vlevo (*true*) nebo budou znaky pouze přeblikávat bez animace (*false*). Bez uvedení parametru *sweep* bude text odjíždět vlevo.
* `trrIsDisplayingText()` - vrací pravdivostní hodnotu (*true* nebo *false*) označující jestli je aktuálně vypisován zadaný text.

Příklad: Následující program při startu vypíše text "TrackRay is starting" v pohyblivém módu textu.
```
#include "TrackRay/TrackRay.h"

void setup() {
    trrBegin();
    trrDisplayText("TrackRay is starting");
}

void loop() {
    delay(500);
}
```

___
## <a name = buzzerCannon>Bzučák a kanón</a>

Pro ovládání bzučáku slouží funkce `trrBuzzerBeep()`. Jako parametr uvedeme délku pípnutí v milisekundách. Následující příkaz pípne bzučákem na půl vteřiny:

`trrBuzzerBeep(500);`

Pro ovládání kanónu můžete použít i funkci `trrCanonShoot()`. Funkce zapne motor kanónu na plný výkon (100) po dobu uvedenou v parametru funkce, obdobně jako u bzučáku. Následující příkaz zapne motor kanónu na 1 vteřinu, což odpovídá přibližně jednomu výstřelu.

`trrCanonShoot();`

___
## <a name = gyroskop>Gyroskop a akcelerometr</a>

### Motivace
Při programování TrackRay je výhodné něco vědět o jeho orientaci v prostoru. Díky tomu budeme moci TrackRay naučit jezdit více samostatně. 

### Orientace v prostoru
V desce elektroniky tvého TrackRay je osazen gyroskop a akcelerometr. 
* **Gyroskop** je senozor, pomocí kterého měříme rychlost otáčení TrackRay podél každé ze 3 prostorových os. 
* **Akcelerometr** je senzor, pomocí kterého měříme pohybové zrychlení TrackRay v každé ze 3 os.

Chytrou kombinací těchto senzorů si dokážeme udělat poměrně dobrou představu o orientaci tvého TrackRay v prostoru. Orientaci TrackRay v prostoru budeme vyjadřovat pomocí 3 úhlů:
* **Yaw** nebo česky klopení.
* **Pitch** nebo česky klonění.
* **Roll** nebo česky bočení.

Orientaci těchto úhlů v prostoru můžeš vidět na obrázku:

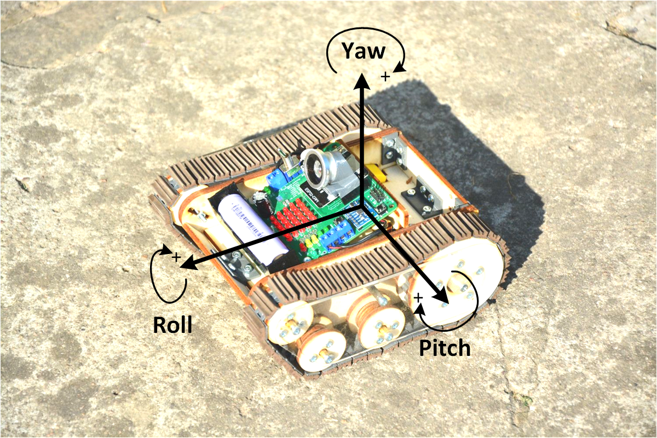
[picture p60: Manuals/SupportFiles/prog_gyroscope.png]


Pro vyčítání dat z gyroskopu budeme používat následující funkce:
* `trrGyroYaw()` - vrátí nám úhel *yaw* v rozsahu -180° až 180°.
* `trrGyroPitch()` - vrátí nám úhel *pitch* v rozsahu -180° až 180°. Na rovné ploše vrací úhel 0°.
* `trrGyroRoll()` - vrátí nám úhel *roll* v rozsahu -180° až 180°. Na rovné ploše vrací úhel 0°.
* `trrGyroData()` - umožňuje vyčíst všechny 3 úhly zaráz.
* `trrGyroEnabled()` - vrátí nám pravdivostní hodnotu `true` nebo `false` podle toho, jestli je senzor správně připojen.
* `trrGyroCalibrate()` - umožňuje kalibrovat gyroskop a akcelerometr.
* `void trrGyroUpdate()` - aktualizuje aktuální hodnoty čtené z gyroskopu a akcelerometru

Příklad: Následující program bude zobrazovat úhly natočení TrackRay do sériové linky:
```
#include "TrackRay/TrackRay.h"

void setup() {
    trrBegin();
}

void loop() {
    trrGyroUpdate();
    printf("%f %f %f\n", trrGyroYaw(), trrGyroPitch(), trrGyroRoll());
    delay(200);
}
```

Příklad: Následující program bude zobrazovat úhly natočení TrackRay do sériové linky pomocí funkce `trrGyroData()`:
```
#include "TrackRay/TrackRay.h"

void setup() {
    trrBegin();
}

void loop() {
    trrGyroUpdate();
    float ypr[3];
    trrGyroData(ypr);
    printf("%f %f %f\n", ypr[0], ypr[1], ypr[2]);
    delay(200);
}
```

### Kalibrace
Gyroskop a akcelerometr tvého TrackRay byl zkalibrován při jeho prvním spuštění. Pokud budeš chtít měřená data senzorů zpřesnit, můžeš provést kalibraci.
1. Umísti TrackRay na podstavec tak, aby deska elektroniky byla vodorovně a nepohybovala se.
1. Příkazem `trrGyroCalibrate();` spustíš kalibraci. Ta může trvat několik minut. Během kalibrace je vypisován stav na sériovou linku.
1. Po ukončení kalibrace jsou vypsány kalibrační hodnoty na sériovou linku a uloženy.

___
## <a name = wifi>Připojení k WiFi</a>
Pro připojení TrackRay k WiFi slouží funkce `trrWiFiControlStart()`. Ta vytvoří vlastní WiFi přístupový bod (AP) dle uvedených přihlašovacích údajů. K tomuto bodu je po zavolání funkce možné se připojit chytrým zařízením, začít ovládat TrackRay a připojit ho k externí WiFi síti. Následující příkaz aktivuje WiFi a vytvoří vlastní WiFi přístupový bod s názvem (SSID) *TrackRay* a heslem *12345678*. Pozor, heslo musí mít minimálně 8 znaků.

`trrWiFiControlStart("TrackRay", "12345678");`

___
## <a name = remoteCmd>Vzdálený příkazový řádek</a>
Pro dálkové ovládání TrackRay můžeš použít i textové příkazy. Ty budeš zadávat do pole *Command entry* na webové stránce dálkového ovládání. Po stisku tlačítka *Enter* (funguje i na klávesnici) je zadaný příkaz odeslán do TrackRay. K použítí přijatého příkazu budeme používat následující funkce:
* `trrCommandGet()` - vrací textový řetězec (proměnnou typu *String*) obsahující aktuálně přijatý příkaz.
* `trrCommandGetIndexed(uint8_t index)` - vrací textový řetězec obsahující jedno slovo z přijatého příkazu. Slova jsou oddělena mezerami a číslována od 0.
* `trrCommandClear()` - vymaže obsah aktuálně přijatého příkazu.

Příklad: Následující program blikne LED reflektorem po obdržení příkazu "flash":
```
#include "TrackRay/TrackRay.h"

void setup() {
    trrBegin();
    trrWiFiControlStart("TrackRay", "12345678");    // password length minimally 8 characters
}

void loop() {
    if(trrCommandGet() == "flash") {
        trrSetFlashLightAnalog(50);
        delay(500);
        trrSetFlashLightAnalog(0);
        trrCommandClear();  // nutné jinak bude v paměti pořád příkaz "flash" a LED bude pořád svítit
    }
    delay(200);
}
```

Příklad: Následující program rozsvítí LED na příkaz "flash on" a zhasne na příkaz "flash off":
```
#include "TrackRay/TrackRay.h"

void setup() {
    trrBegin();
    trrWiFiControlStart("TrackRay", "12345678");    // password length minimally 8 characters
}

void loop() {
    if(trrCommandGetIndexed(0) == "flash") {
        if(trrCommandGetIndexed(1) == "on") {
            trrSetFlashLightAnalog(50);
        }
        else if(trrCommandGetIndexed(1) == "off") {
            trrSetFlashLightAnalog(0);
        }
        trrCommandClear();
    }
    delay(200);
}
```

TrackRay umožňuje textovou komunikaci i opačným směrem, tedy z TrackRay do webové stránky dálkového ovládání.
* `trrCommandSend(String command)` - odešle textový příkaz z TrackRay a zobrazí ho šedě v poli *Command entry*.

Příklad: Následující program bude v textovém poli *Command entry* vypisovat stav tlačítka TrackRay:
```
#include "TrackRay/TrackRay.h"

void setup() {
    trrBegin();
    trrWiFiControlStart("TrackRay", "12345678");    // password length minimally 8 characters
}

void loop() {
    trrCommandSend(String(trrReadButton()));
    delay(200);
}
```

___
## <a name = kamera>Kamera</a>
Pro používání kamery je možné použít následující funkce:
* `trrCamEnable();` - aktivuje přenos obrazu do webové stránky dálkového ovládání. Pokud není kamera připojena, nic se nestane.
* `trrCamDisable();` - deaktivuje přenos obrazu.

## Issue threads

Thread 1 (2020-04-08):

Serial programming does not work when I2C pullup connected

marouncz, 2020-04-08:
In H00, I2C pullup resistor is connected to IO2, which does not allow ESP32 to boot into programming mode.
This issue is to be fixed in H01

marouncz, 2020-05-03:
SDA and REG_DAT swapped in H01

Closed 2020-05-03.

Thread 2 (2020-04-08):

Battery indicator has wrong range

marouncz, 2020-04-08:
In H00, resistors, that serve as voltage reference for battery indicator have wrong values. They need a bit more fine-tuning.
This issue is to be fixed in H01.

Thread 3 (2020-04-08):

Wrong LED color for charging indication

marouncz, 2020-04-08:
In H00, D31 and D32 have swapped colors. This results in wrong charging indication status.
The text in schematic is to be swapped in H01.

marouncz, 2020-05-03:
Description fixed.

Closed 2020-05-03.

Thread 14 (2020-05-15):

Add flyback diode for M3

marouncz, 2020-05-15:
A flyback diode should be added parallel to M3, if inductive load (i. e. motor) is connected. Also a beefier MOSFET should be considered with motor type in mind.

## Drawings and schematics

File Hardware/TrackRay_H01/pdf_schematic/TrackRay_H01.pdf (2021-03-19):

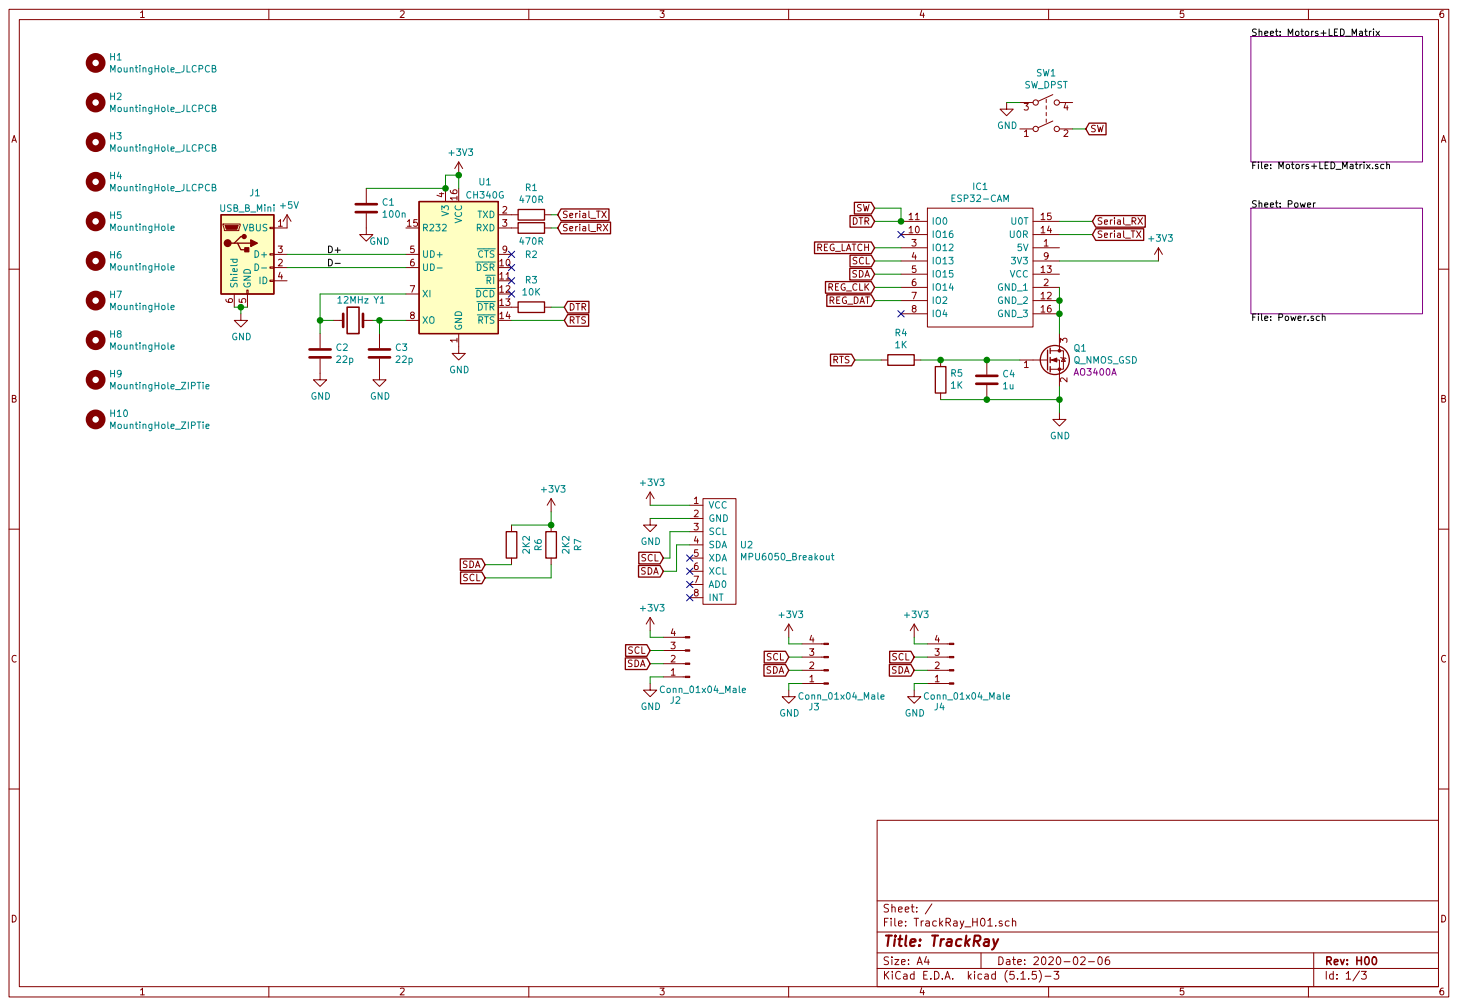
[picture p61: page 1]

Sheet: Motors+LED_Matrix File: Motors+LED_Matrix.sch Sheet: Power File: Power.sch
SCL Serial_RX

4 UD+ 5 UD- 6 XI 7 XO 8 CTS 9 U1 CH340G

1 DSR 10 RI 11 DCD 12 DTR 13 RTS 14 R232 15 VCC 16 TXD 2 RXD 3 V3

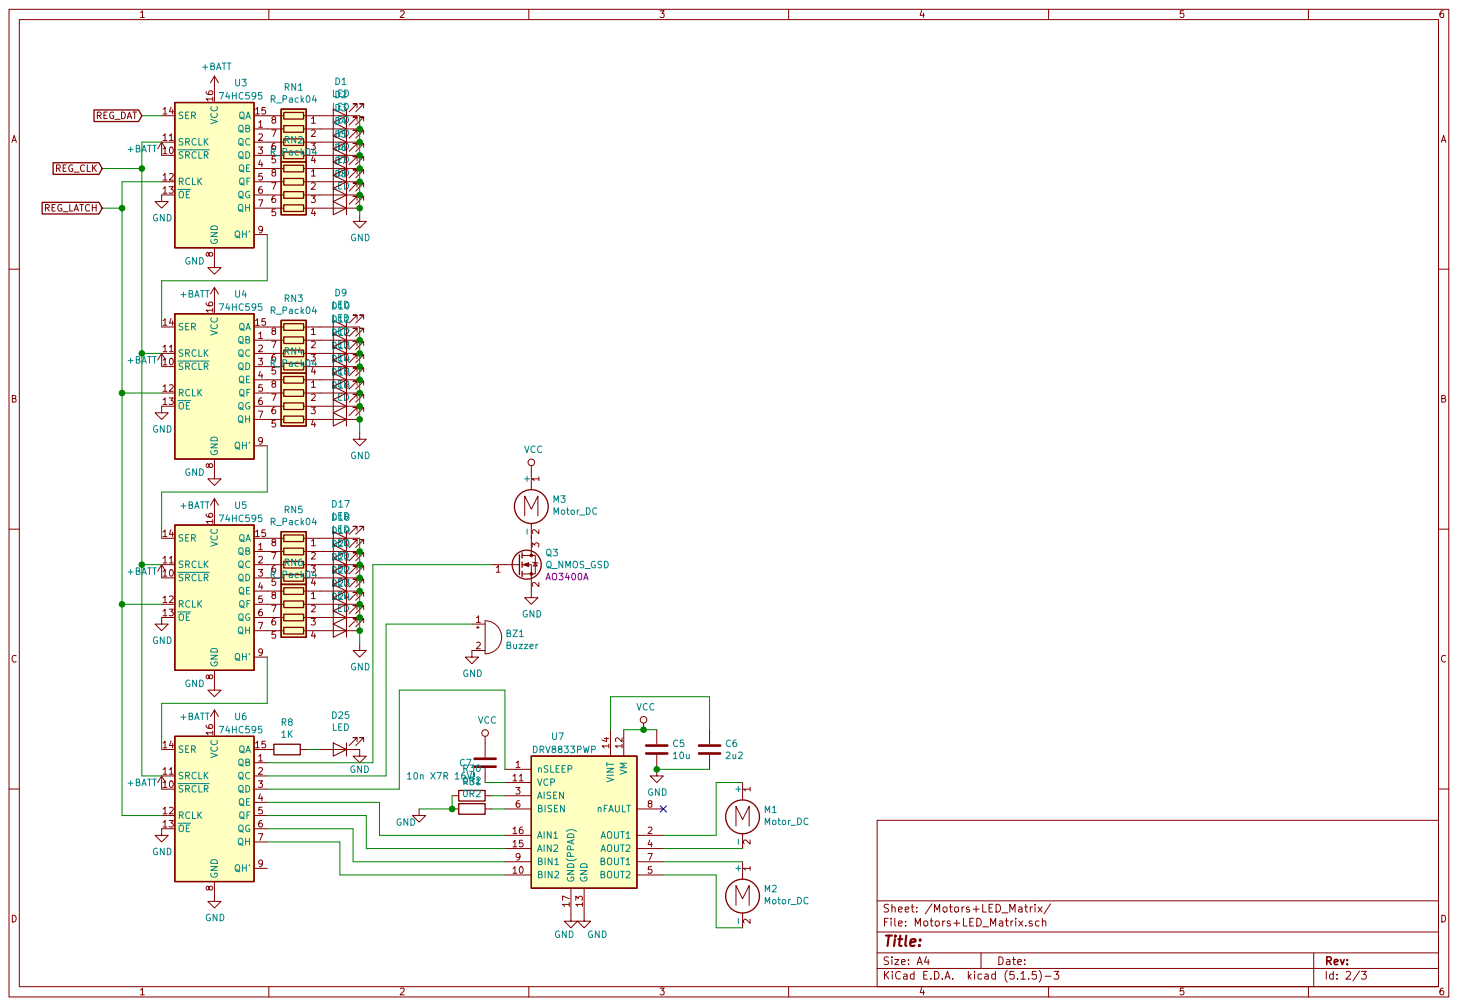
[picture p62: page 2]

LED D6
LED D7
LED D8
LED

LED D12
LED D13
LED D14
LED D15
LED D16

LED D20
LED D21
D22
LED D23
LED D24

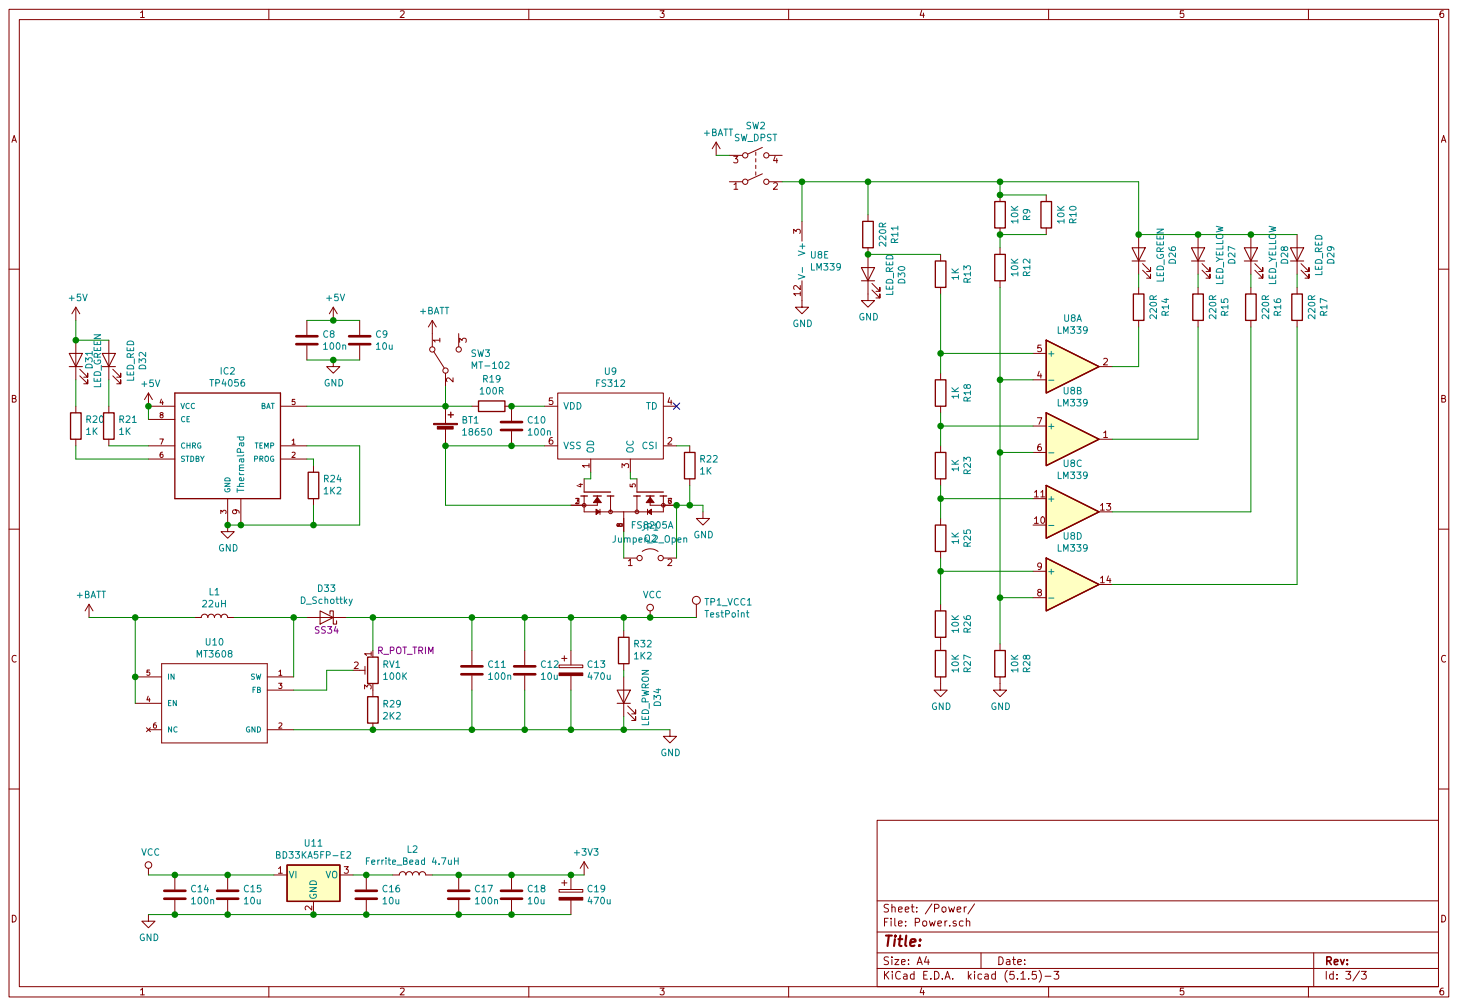
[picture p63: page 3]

3 VCC 4 BAT 5 STDBY 6 CHRG 7 CE 8 ThermalPad

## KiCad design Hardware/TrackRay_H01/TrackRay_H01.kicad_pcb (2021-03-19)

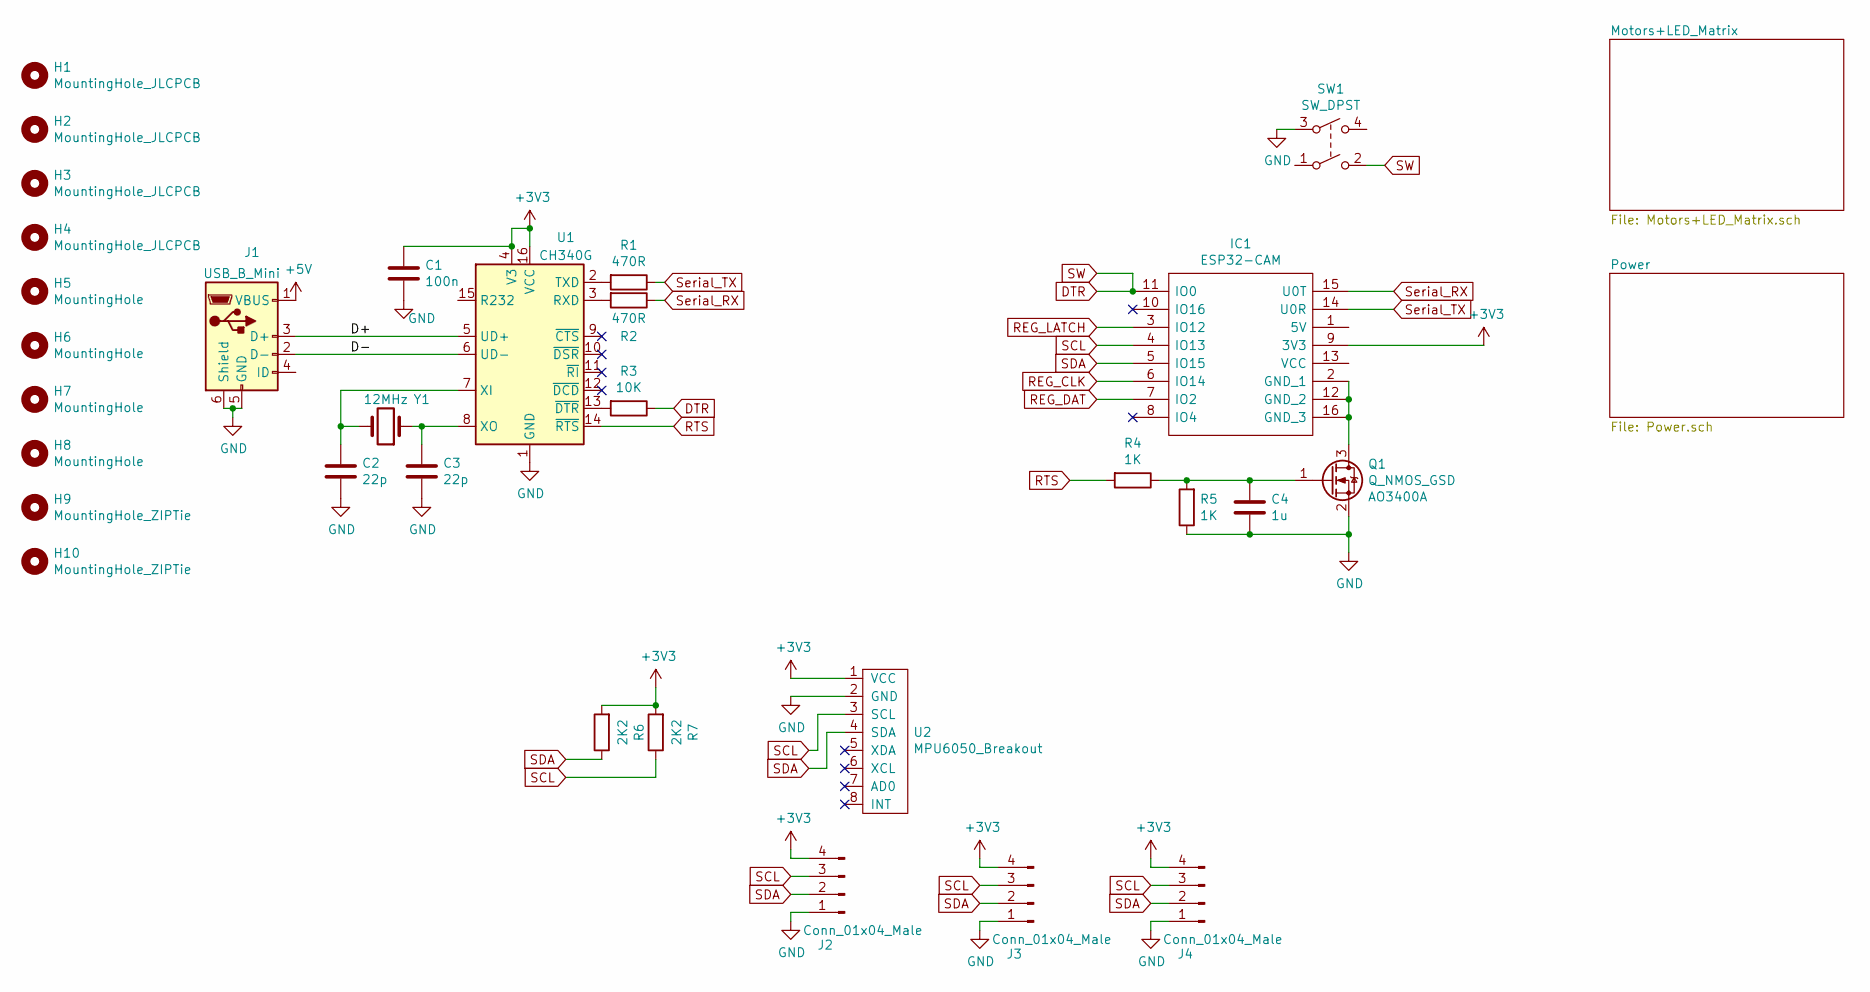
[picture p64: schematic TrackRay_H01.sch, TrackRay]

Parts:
C1: 100n; C_0805_2012Metric
C2, C3: 22p; C_0805_2012Metric
C4: 1u; C_0805_2012Metric
H1, H2, H3, H4: MountingHole_JLCPCB; JLCPCB_ToolingHole
H5, H6, H7, H8: MountingHole; MountingHole_3.2mm_M3
H9, H10: MountingHole_ZIPTie; ZIP_Tie_Slot_Hole
IC1: ESP32-CAM
J1: USB_B_Mini; USB_MINIB
J2, J3, J4: Conn_01x04_Male; PinHeader_1x04_P2.54mm_Vertical
Q1: Q_NMOS_GSD; SOT-23; LCSC C20917
R1, R2: 470R; R_0805_2012Metric
R3: 10K; R_0805_2012Metric
R4, R5: 1K; R_0805_2012Metric
R6, R7: 2K2; R_0805_2012Metric
SW1: SW_DPST; SW_TH_Tactile_Omron_B3F-10xx
U1: CH340G; SOIC-16_3.9x9.9mm_P1.27mm
U2: MPU6050_Breakout; MPU6050_Breakdown
Y1: 12MHz; Crystal_HC49-4H_Vertical

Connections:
+3V3: C1.1, IC1.9 (3V3), J2.4, J3.4, J4.4, R6.2, R7.2, U1.4 (V3), U1.16 (VCC), U2.1 (VCC); also elsewhere on the board
+5V: J1.1 (VBUS); also elsewhere on the board
/D+: J1.3 (D+), U1.5 (UD+)
/D-: J1.2 (D-), U1.6 (UD-)
DTR: IC1.11 (IO0), R3.1, SW1.2
GND: C1.2, C2.2, C3.2, C4.2, J1.5 (GND), J1.6 (Shield), J2.1, J3.1, J4.1, Q1.2 (S), R5.1, SW1.3, U1.1 (GND), U2.2 (GND); also elsewhere on the board
unnamed: C2.1, U1.7 (XI), Y1.2
unnamed: C3.1, U1.8 (XO), Y1.1
unnamed: C4.1, Q1.1 (G), R4.1, R5.2
unnamed: IC1.2 (GND_1), IC1.12 (GND_2), IC1.16 (GND_3), Q1.3 (D)
unnamed: R1.2, U1.2 (TXD)
unnamed: R2.2, U1.3 (RXD)
unnamed: R3.2, U1.13 (~DTR)
REG_CLK: IC1.6 (IO14); also elsewhere on the board
REG_DAT: IC1.7 (IO2); also elsewhere on the board
REG_LATCH: IC1.3 (IO12); also elsewhere on the board
RTS: R4.2, U1.14 (~RTS)
SCL: IC1.4 (IO13), J2.3, J3.3, J4.3, R7.1, U2.3 (SCL)
SDA: IC1.5 (IO15), J2.2, J3.2, J4.2, R6.1, U2.4 (SDA)
Serial_RX: IC1.15 (U0T), R2.1
Serial_TX: IC1.14 (U0R), R1.1

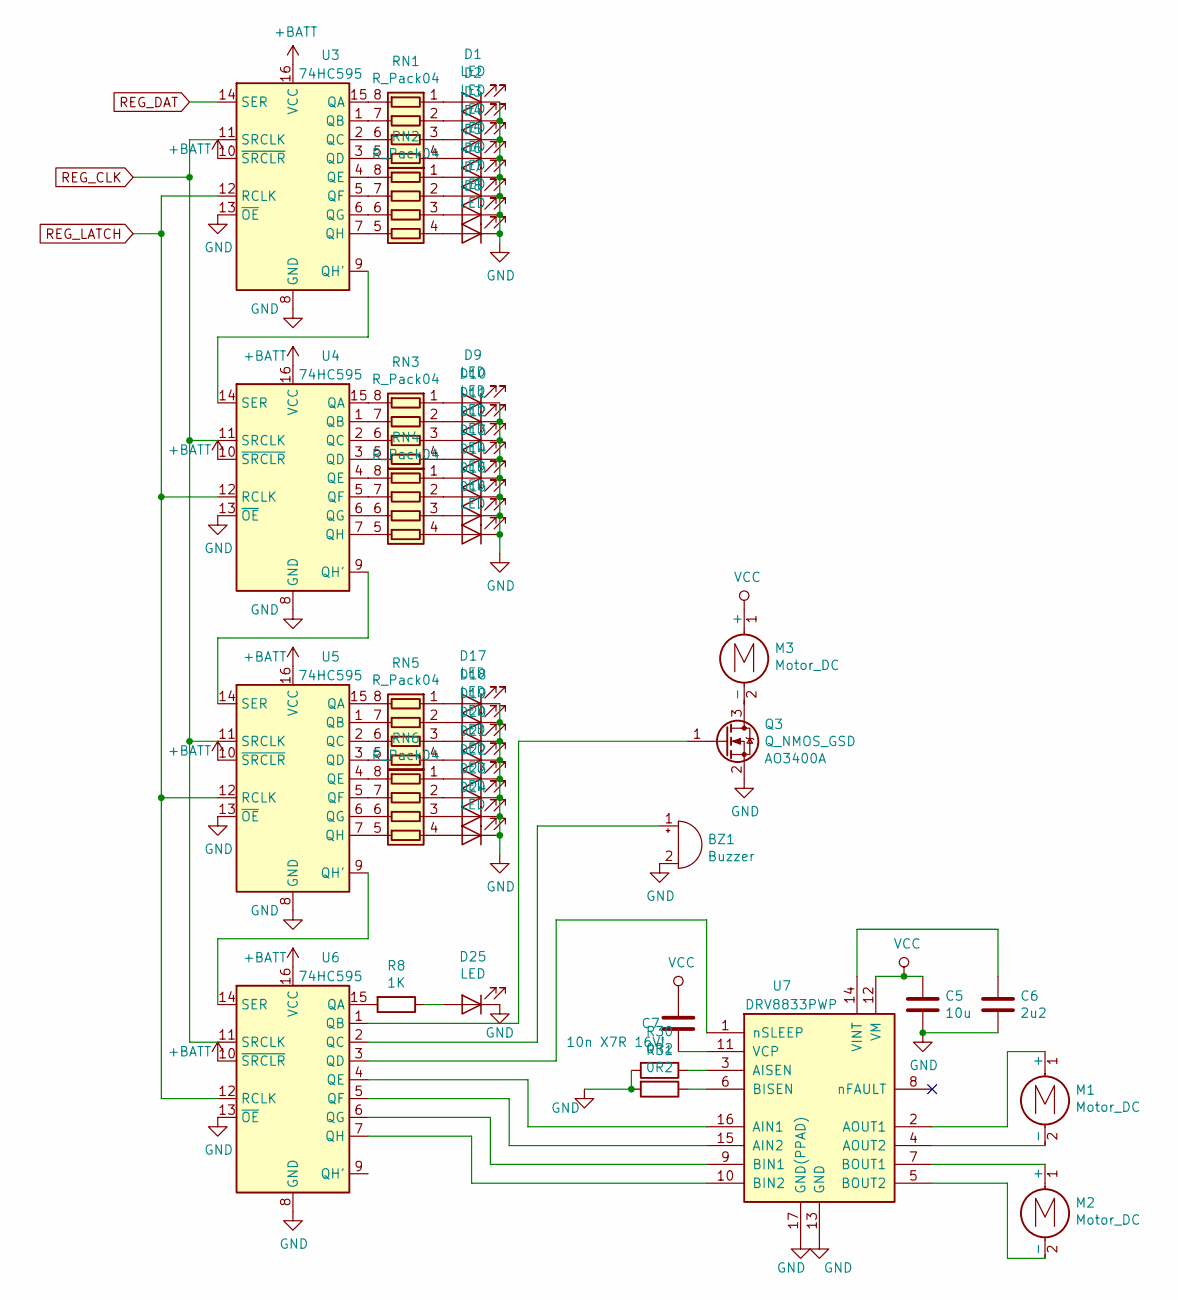
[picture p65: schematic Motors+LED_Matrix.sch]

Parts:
BZ1: Buzzer; Buzzer_12x9.5RM7.6
C5: 10u; C_0805_2012Metric
C6: 2u2; C_0805_2012Metric
C7: 10n X7R 16V!; C_0805_2012Metric
D1, D2, D3, D4, D5, D6, D7, D8, D9, D10, D11, D12, D13, D14, D15, D16, D17, D18, D19, D20, D21, D22, D23, D24, D25: LED; LED_D3.0mm
M1, M2, M3: Motor_DC; TerminalBlock_RND_205-00012_1x02_P5.00mm_Horizontal
Q3: Q_NMOS_GSD; SOT-23; LCSC C20917
R8: 1K; R_0805_2012Metric
R30, R31: 0R2; R_1206_3216Metric
RN1, RN2, RN3, RN4, RN5, RN6: R_Pack04; R_Array_Convex_4x0603
U3, U4, U5, U6: 74HC595; SOIC-16_3.9x9.9mm_P1.27mm
U7: DRV8833PWP; HTSSOP-16-1EP_4.4x5mm_P0.65mm_EP3.4x5mm_Mask2.46x2.31mm_The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

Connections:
+BATT: U3.10 (~SRCLR), U3.16 (VCC), U4.10 (~SRCLR), U4.16 (VCC), U5.10 (~SRCLR), U5.16 (VCC), U6.10 (~SRCLR), U6.16 (VCC); also elsewhere on the board
GND: BZ1.2 (+), C5.2, C6.2, D1.1 (K), D2.1 (K), D3.1 (K), D4.1 (K), D5.1 (K), D6.1 (K), D7.1 (K), D8.1 (K), D9.1 (K), D10.1 (K), D11.1 (K), D12.1 (K), D13.1 (K), D14.1 (K), D15.1 (K), D16.1 (K), D17.1 (K), D18.1 (K), D19.1 (K), D20.1 (K), D21.1 (K), D22.1 (K), D23.1 (K), D24.1 (K), D25.1 (K), Q3.2 (S), R30.2, R31.2, U3.8 (GND), U3.13 (~OE), U4.8 (GND), U4.13 (~OE), U5.8 (GND), U5.13 (~OE), U6.8 (GND), U6.13 (~OE), U7.13 (GND), U7.17 (GND(PPAD)); also elsewhere on the board
unnamed: BZ1.1 (-), U6.2 (QC)
unnamed: C6.1, U7.14 (VINT)
unnamed: C7.2, U7.11 (VCP)
unnamed: D1.2 (A), RN1.1 (R1.1)
unnamed: D2.2 (A), RN1.2 (R2.1)
unnamed: D3.2 (A), RN1.3 (R3.1)
unnamed: D4.2 (A), RN1.4 (R4.1)
unnamed: D5.2 (A), RN2.1 (R1.1)
unnamed: D6.2 (A), RN2.2 (R2.1)
unnamed: D7.2 (A), RN2.3 (R3.1)
unnamed: D8.2 (A), RN2.4 (R4.1)
unnamed: D9.2 (A), RN3.1 (R1.1)
unnamed: D10.2 (A), RN3.2 (R2.1)
unnamed: D11.2 (A), RN3.3 (R3.1)
unnamed: D12.2 (A), RN3.4 (R4.1)
unnamed: D13.2 (A), RN4.1 (R1.1)
unnamed: D14.2 (A), RN4.2 (R2.1)
unnamed: D15.2 (A), RN4.3 (R3.1)
unnamed: D16.2 (A), RN4.4 (R4.1)
unnamed: D17.2 (A), RN5.1 (R1.1)
unnamed: D18.2 (A), RN5.2 (R2.1)
unnamed: D19.2 (A), RN5.3 (R3.1)
unnamed: D20.2 (A), RN5.4 (R4.1)
unnamed: D21.2 (A), RN6.1 (R1.1)
unnamed: D22.2 (A), RN6.2 (R2.1)
unnamed: D23.2 (A), RN6.3 (R3.1)
unnamed: D24.2 (A), RN6.4 (R4.1)
unnamed: D25.2 (A), R8.1
unnamed: M1.1 (+), U7.2 (AOUT1)
unnamed: M1.2 (-), U7.4 (AOUT2)
unnamed: M2.1 (+), U7.7 (BOUT1)
unnamed: M2.2 (-), U7.5 (BOUT2)
unnamed: M3.2 (-), Q3.3 (D)
unnamed: Q3.1 (G), U6.1 (QB)
unnamed: R8.2, U6.15 (QA)
unnamed: R30.1, U7.3 (AISEN)
unnamed: R31.1, U7.6 (BISEN)
unnamed: RN1.5 (R4.2), U3.3 (QD)
unnamed: RN1.6 (R3.2), U3.2 (QC)
unnamed: RN1.7 (R2.2), U3.1 (QB)
unnamed: RN1.8 (R1.2), U3.15 (QA)
unnamed: RN2.5 (R4.2), U3.7 (QH)
unnamed: RN2.6 (R3.2), U3.6 (QG)
unnamed: RN2.7 (R2.2), U3.5 (QF)
unnamed: RN2.8 (R1.2), U3.4 (QE)
unnamed: RN3.5 (R4.2), U4.3 (QD)
unnamed: RN3.6 (R3.2), U4.2 (QC)
unnamed: RN3.7 (R2.2), U4.1 (QB)
unnamed: RN3.8 (R1.2), U4.15 (QA)
unnamed: RN4.5 (R4.2), U4.7 (QH)
unnamed: RN4.6 (R3.2), U4.6 (QG)
unnamed: RN4.7 (R2.2), U4.5 (QF)
unnamed: RN4.8 (R1.2), U4.4 (QE)
unnamed: RN5.5 (R4.2), U5.3 (QD)
unnamed: RN5.6 (R3.2), U5.2 (QC)
unnamed: RN5.7 (R2.2), U5.1 (QB)
unnamed: RN5.8 (R1.2), U5.15 (QA)
unnamed: RN6.5 (R4.2), U5.7 (QH)
unnamed: RN6.6 (R3.2), U5.6 (QG)
unnamed: RN6.7 (R2.2), U5.5 (QF)
unnamed: RN6.8 (R1.2), U5.4 (QE)
unnamed: U3.9 (QH'), U4.14 (SER)
unnamed: U4.9 (QH'), U5.14 (SER)
unnamed: U5.9 (QH'), U6.14 (SER)
unnamed: U6.3 (QD), U7.1 (nSLEEP)
unnamed: U6.4 (QE), U7.16 (AIN1)
unnamed: U6.5 (QF), U7.15 (AIN2)
unnamed: U6.6 (QG), U7.9 (BIN1)
unnamed: U6.7 (QH), U7.10 (BIN2)
REG_CLK: U3.11 (SRCLK), U4.11 (SRCLK), U5.11 (SRCLK), U6.11 (SRCLK); also elsewhere on the board
REG_DAT: U3.14 (SER); also elsewhere on the board
REG_LATCH: U3.12 (RCLK), U4.12 (RCLK), U5.12 (RCLK), U6.12 (RCLK); also elsewhere on the board
VCC: C5.1, C7.1, M3.1 (+), U7.12 (VM); also elsewhere on the board

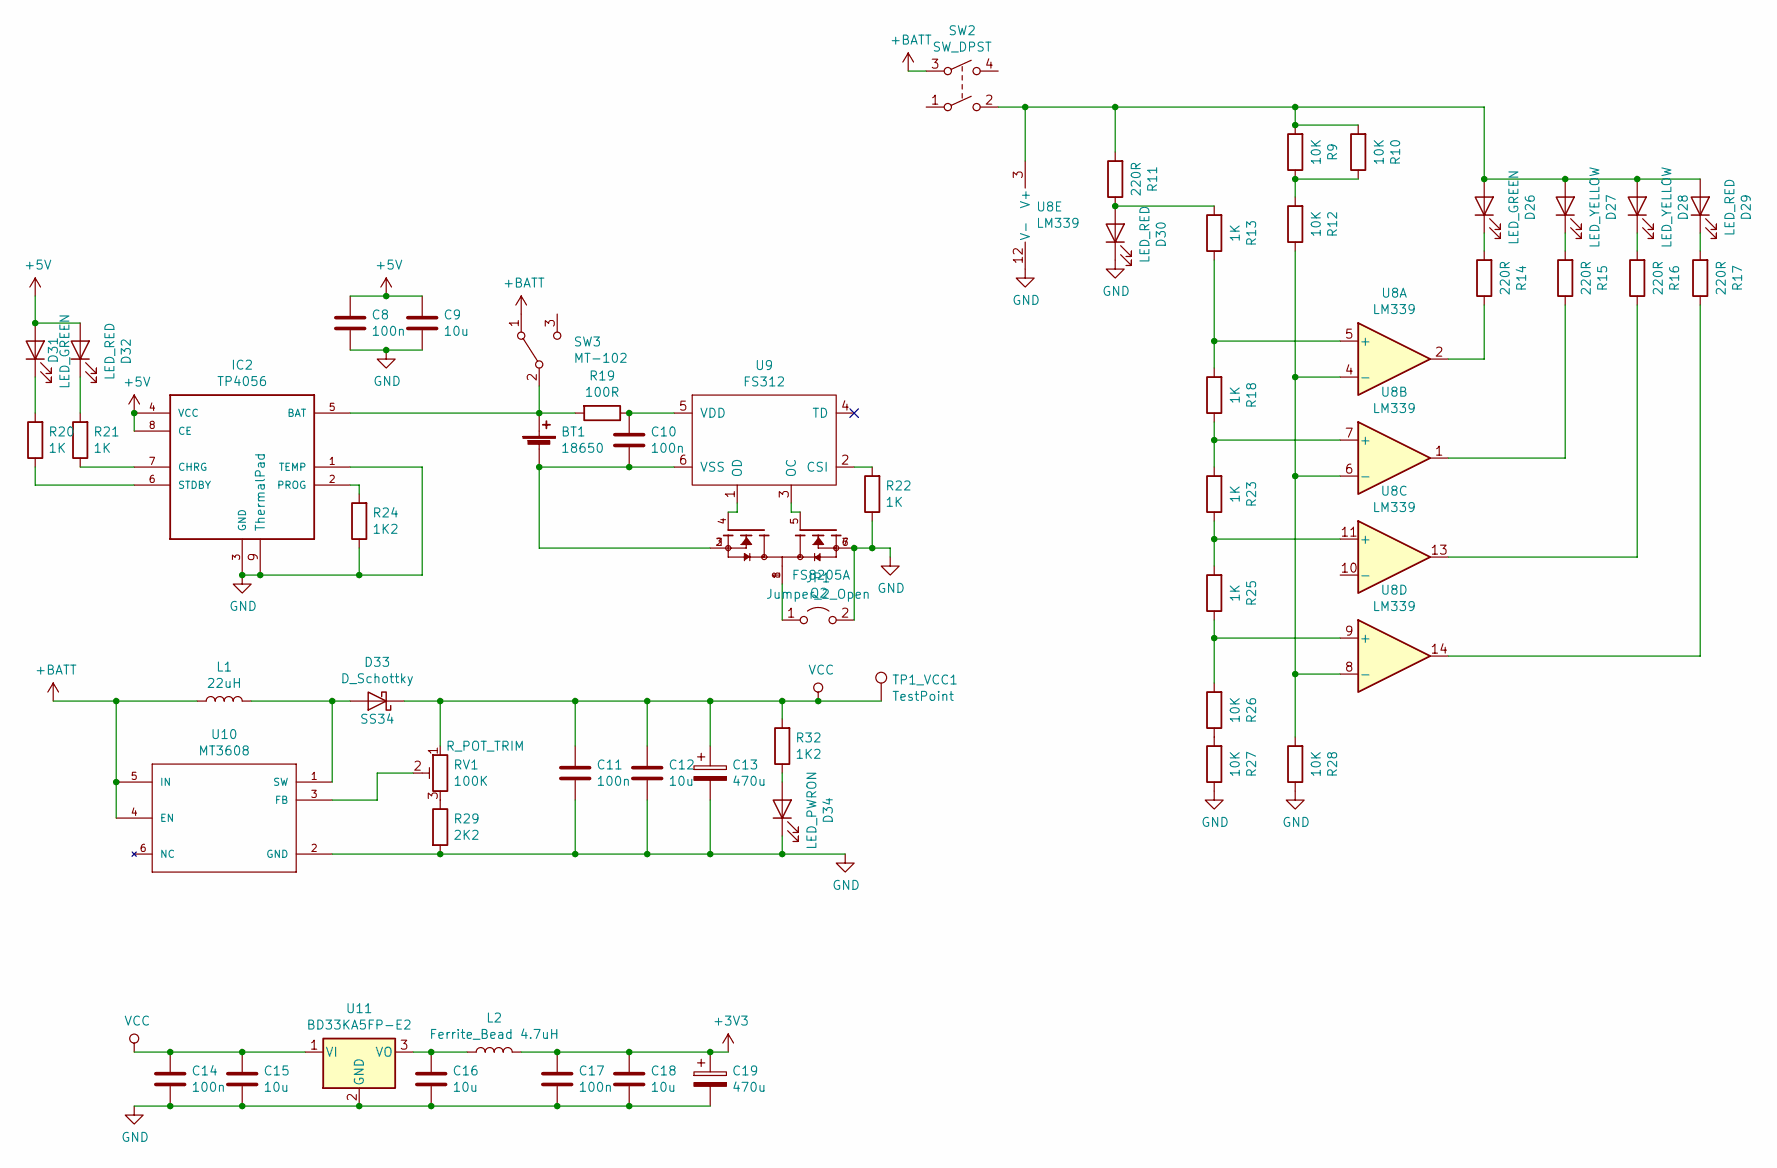
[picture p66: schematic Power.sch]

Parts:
BT1: 18650; BatteryHolder_MPD_BH-18650-PC2
C8, C10, C11, C14, C17: 100n; C_0805_2012Metric
C9, C12, C15, C16, C18: 10u; C_0805_2012Metric
C13, C19: 470u; CP_Radial_D10.0mm_P5.00mm
D26, D31: LED_GREEN; LED_D3.0mm
D27, D28: LED_YELLOW; LED_D3.0mm
D29, D30, D32: LED_RED; LED_D3.0mm
D33: D_Schottky; D_SMA; LCSC C8678
D34: LED_PWRON; LED_D3.0mm
IC2: TP4056; SOIC-8-1EP_3.9x4.9mm_P1.27mm_EP2.514x3.2mm_ThermalVias
JP1: Jumper_2_Open; SolderJumper-2_P1.3mm_Open_TrianglePad1.0x1.5mm
L1: 22uH; L_12x12mm_H6mm; LCSC C169385
L2: Ferrite_Bead 4.7uH; L_1206_3216Metric; LCSC2 C1049
Q2: FS8205A; TSSOP-8_4.4x3mm_P0.65mm
R9, R10, R12, R26, R27, R28: 10K; R_0805_2012Metric
R11, R14, R15, R16, R17: 220R; R_0805_2012Metric
R13, R18, R20, R21, R22, R23, R25: 1K; R_0805_2012Metric
R19: 100R; R_0805_2012Metric
R24, R32: 1K2; R_0805_2012Metric
R29: 2K2; R_0805_2012Metric
RV1: 100K; Potentiometer_Bourns_3296W_Vertical
SW2: SW_DPST; SW_TH_Tactile_Omron_B3F-10xx
SW3: MT-102; TE_A101SYCQ04
TP1_VCC1: TestPoint; TestPoint_THTPad_D2.0mm_Drill1.0mm
U8: LM339; TSSOP-14_4.4x5mm_P0.65mm
U9: FS312; SOT-23-6
U10: MT3608; SOT-23-6
U11: BD33KA5FP-E2; TO-252-3_TabPin2

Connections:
+3V3: C17.1, C18.1, C19.1, L2.2; also elsewhere on the board
+5V: C8.1, C9.1, D31.2 (A), D32.2 (A), IC2.4 (VCC), IC2.8 (CE); also elsewhere on the board
+BATT: L1.1, SW2.3, SW3.1 (A), U10.4 (EN), U10.5 (IN); also elsewhere on the board
GND: C8.2, C9.2, C11.2, C12.2, C13.2, C14.2, C15.2, C16.2, C17.2, C18.2, C19.2, D30.1 (K), D34.1 (K), IC2.1 (TEMP), IC2.3 (GND), IC2.9 (ThermalPad), JP1.2 (B), Q2.6 (S2), Q2.7 (S2), R22.1, R24.1, R27.1, R28.1, R29.2, U8.12 (V-), U10.2 (GND), U11.2 (GND); also elsewhere on the board
unnamed: BT1.1 (+), IC2.5 (BAT), R19.2, SW3.2 (B)
unnamed: BT1.2 (-), C10.2, Q2.2 (S1), Q2.3 (S1), U9.6 (VSS)
unnamed: C10.1, R19.1, U9.5 (VDD)
unnamed: C16.1, L2.1, U11.3 (VO)
unnamed: D26.1 (K), R14.2
unnamed: D26.2 (A), D27.2 (A), D28.2 (A), D29.2 (A), R9.2, R10.2, R11.2, SW2.2, U8.3 (V+)
unnamed: D27.1 (K), R15.2
unnamed: D28.1 (K), R16.2
unnamed: D29.1 (K), R17.2
unnamed: D30.2 (A), R11.1, R13.2
unnamed: D31.1 (K), R20.2
unnamed: D32.1 (K), R21.2
unnamed: D33.2 (A), L1.2, U10.1 (SW)
unnamed: D34.2 (A), R32.1
unnamed: IC2.2 (PROG), R24.2
unnamed: IC2.6 (STDBY), R20.1
unnamed: IC2.7 (CHRG), R21.1
unnamed: JP1.1 (A), Q2.1 (D12), Q2.8 (D12)
unnamed: Q2.4 (G1), U9.1 (OD)
unnamed: Q2.5 (G2), U9.3 (OC)
unnamed: R9.1, R10.1, R12.2
unnamed: R12.1, R28.2, U8.4 (-), U8.6 (-), U8.8 (-)
unnamed: R13.1, R18.2, U8.5 (+)
unnamed: R14.1, U8.2
unnamed: R15.1, U8.1
unnamed: R16.1, U8.13
unnamed: R17.1, U8.14
unnamed: R18.1, R23.2, U8.7 (+)
unnamed: R22.2, U9.2 (CSI)
unnamed: R23.1, R25.2, U8.11 (+)
unnamed: R25.1, R26.2, U8.9 (+)
unnamed: R26.1, R27.2
unnamed: R29.1, RV1.3
unnamed: RV1.2, U10.3 (FB)
VCC: C11.1, C12.1, C13.1, C14.1, C15.1, D33.1 (K), R32.2, RV1.1, TP1_VCC1.1, U11.1 (VI); also elsewhere on the board

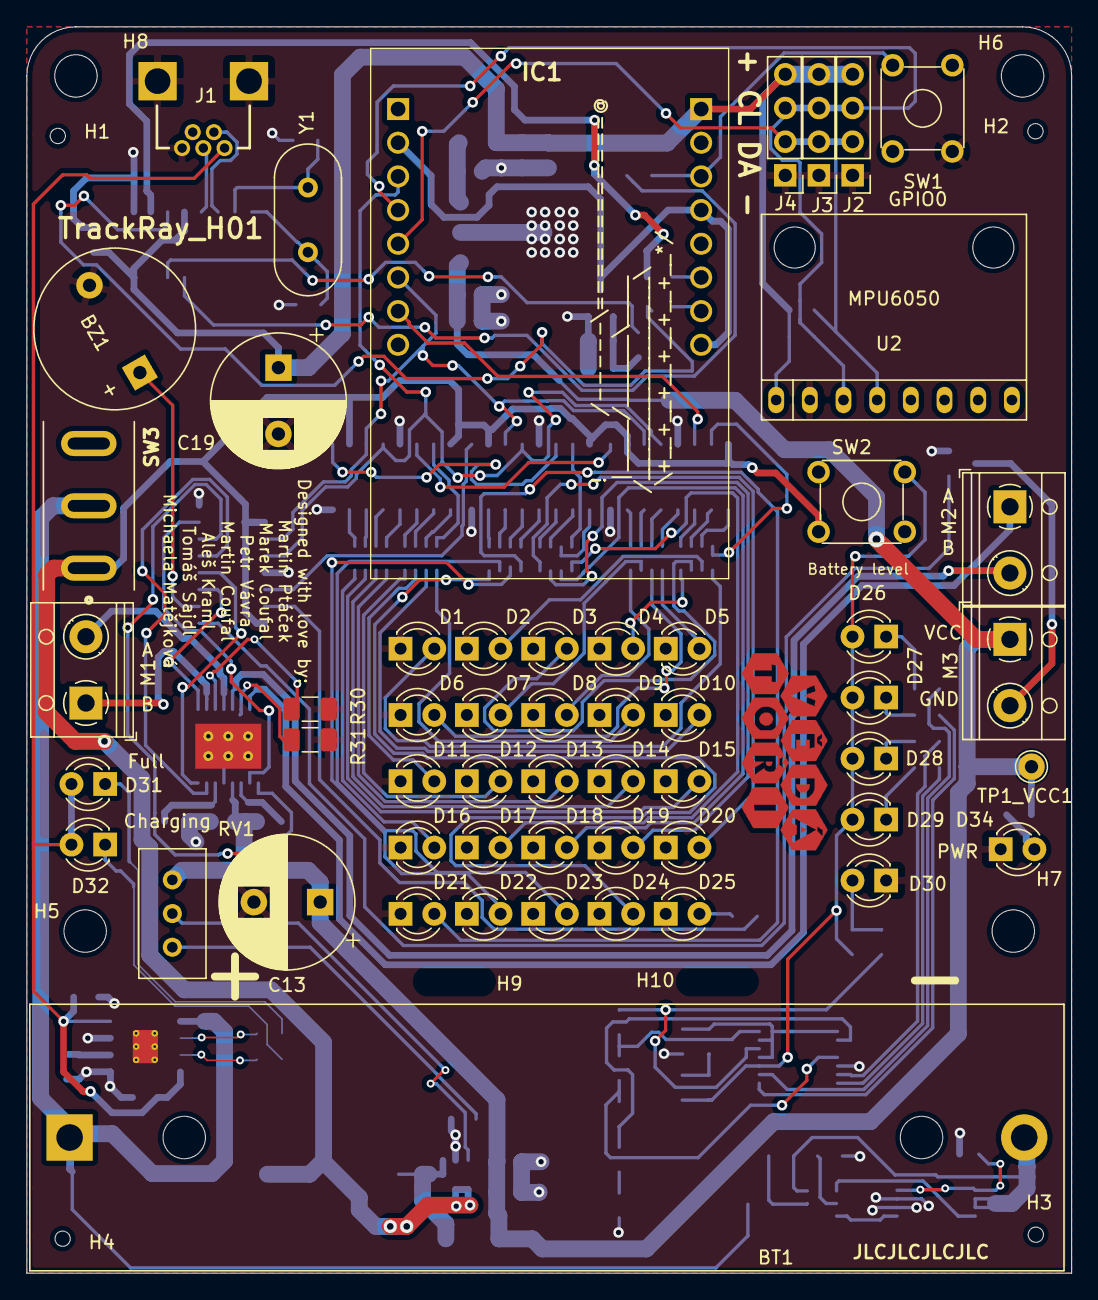
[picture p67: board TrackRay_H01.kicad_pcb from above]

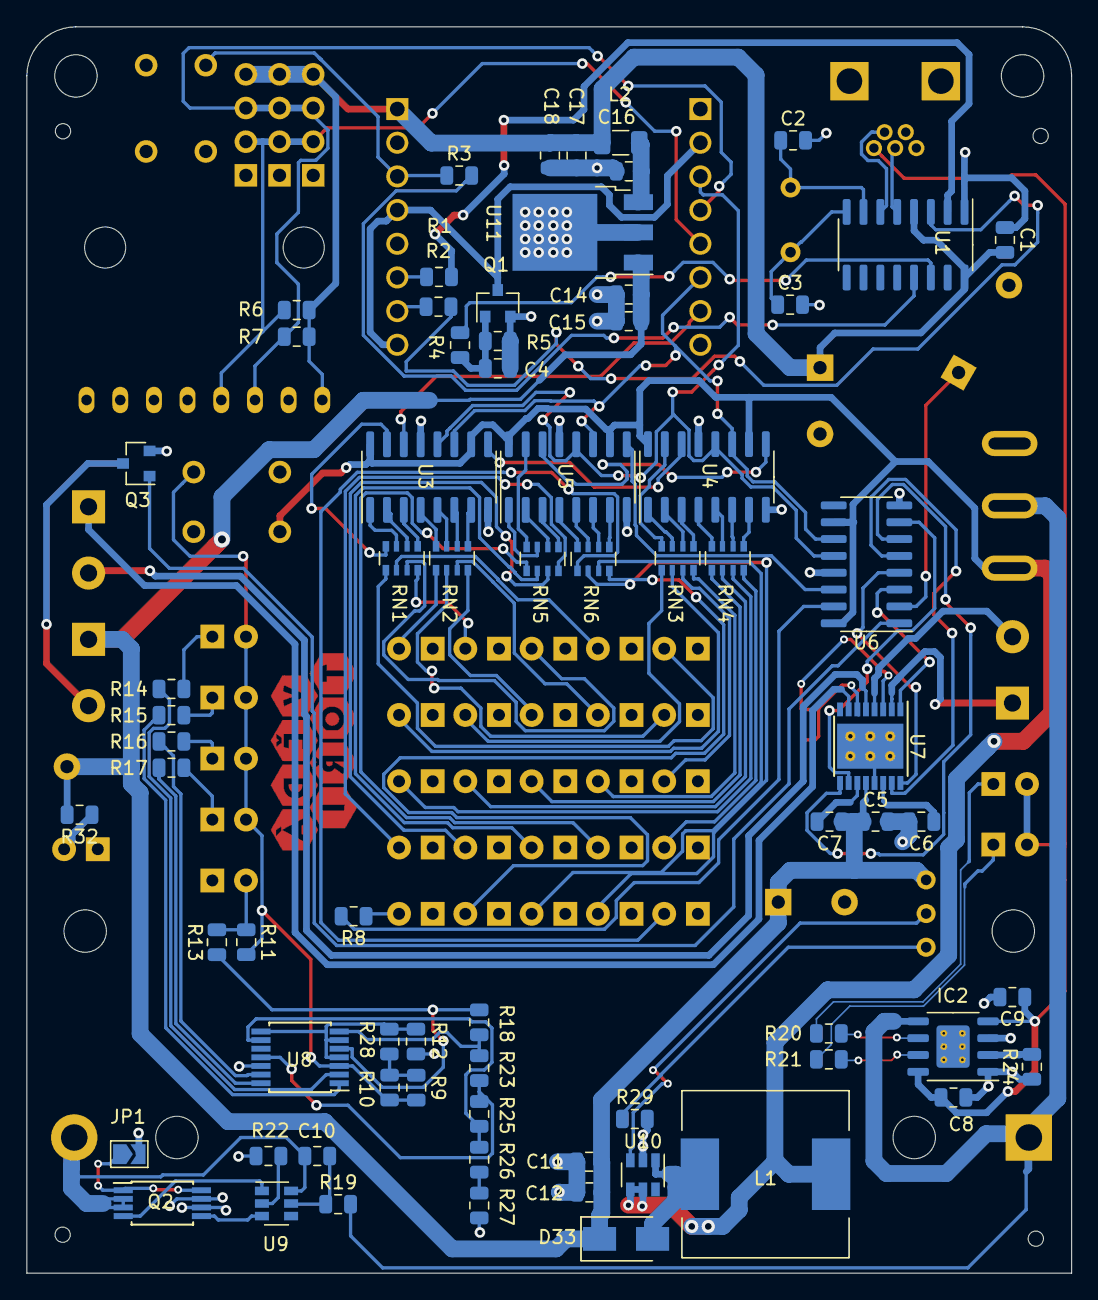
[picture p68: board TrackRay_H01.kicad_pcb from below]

Board: 2 copper layers, 78.8 x 94.0 mm, 136 parts (71 on the bottom side), 126 nets.

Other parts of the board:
.: .; Vedatori_copper_exposed_15mm

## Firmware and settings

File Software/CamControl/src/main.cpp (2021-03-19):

#include <Arduino.h>
#include <ArduinoWebsockets.h>
#include <WiFi.h>
#include "SPIFFS.h"
#include "esp_camera.h"
#include <WebServer.h>

#include "credentials.h"

#define PWDN_GPIO_NUM     32
#define RESET_GPIO_NUM    -1
#define XCLK_GPIO_NUM      0
#define SIOD_GPIO_NUM     26
#define SIOC_GPIO_NUM     27

#define Y9_GPIO_NUM       35
#define Y8_GPIO_NUM       34
#define Y7_GPIO_NUM       39
#define Y6_GPIO_NUM       36
#define Y5_GPIO_NUM       21
#define Y4_GPIO_NUM       19
#define Y3_GPIO_NUM       18
#define Y2_GPIO_NUM        5
#define VSYNC_GPIO_NUM    25
#define HREF_GPIO_NUM     23
#define PCLK_GPIO_NUM     22
 
camera_fb_t * fb = NULL;

websockets::WebsocketsServer server;
WebServer webserver(80);

void handleClients(void * param) {
    for(;;) {
        webserver.handleClient();
        vTaskDelay(200);
    }
}
 
void setup() {

    Serial.begin(115200);
    digitalWrite(4, 0);
    Serial.println("New start");
    
    camera_config_t config;
    config.ledc_channel = LEDC_CHANNEL_0;
    config.ledc_timer = LEDC_TIMER_0;
    config.pin_d0 = Y2_GPIO_NUM;
    config.pin_d1 = Y3_GPIO_NUM;
    config.pin_d2 = Y4_GPIO_NUM;
    config.pin_d3 = Y5_GPIO_NUM;
    config.pin_d4 = Y6_GPIO_NUM;
    config.pin_d5 = Y7_GPIO_NUM;
    config.pin_d6 = Y8_GPIO_NUM;
    config.pin_d7 = Y9_GPIO_NUM;
    config.pin_xclk = XCLK_GPIO_NUM;
    config.pin_pclk = PCLK_GPIO_NUM;
    config.pin_vsync = VSYNC_GPIO_NUM;
    config.pin_href = HREF_GPIO_NUM;
    config.pin_sscb_sda = SIOD_GPIO_NUM;
    config.pin_sscb_scl = SIOC_GPIO_NUM;
    config.pin_pwdn = PWDN_GPIO_NUM;
    config.pin_reset = RESET_GPIO_NUM;
    config.xclk_freq_hz = 20000000;
    config.pixel_format = PIXFORMAT_JPEG;
    //init with high specs to pre-allocate larger buffers
    if (psramFound()) {
        config.frame_size = FRAMESIZE_HQVGA;
        config.jpeg_quality = 10;
        config.fb_count = 2;
    } else {
        config.frame_size = FRAMESIZE_HQVGA;
        config.jpeg_quality = 10;
        config.fb_count = 1;
    }
     
    // camera init
    esp_err_t err = esp_camera_init(&config);
    if (err != ESP_OK) {
        Serial.printf("Camera init failed with error 0x%x", err);
        return;
    }
    
    sensor_t * s = esp_camera_sensor_get();
    //initial sensors are flipped vertically and colors are a bit saturated
    if (s->id.PID == OV3660_PID) {
        s->set_vflip(s, 1);//flip it back
        s->set_brightness(s, 1);//up the blightness just a bit
        s->set_saturation(s, -2);//lower the saturation
    }
    //drop down frame size for higher initial frame rate
    s->set_framesize(s, FRAMESIZE_HQVGA);

    // Connect to wifi
    WiFi.begin(ssid, password);

    // Wait some time to connect to wifi
    for (int i = 0; i < 15 && WiFi.status() != WL_CONNECTED; i++) {
        Serial.print(".");
        delay(1000);
    }

    Serial.print("WiFi connected. IP address: ");
    Serial.println(WiFi.localIP());   // You can get IP address assigned to ESP

    if (!SPIFFS.begin()) {
        Serial.println("SPIFFS Mount failed");
    } 
    else {
        Serial.println("SPIFFS Mount succesfull");
    }
    
    webserver.serveStatic("/", SPIFFS, "/webApp.html");
    
    webserver.begin();
    server.listen(82);

    xTaskCreate(handleClients, "handleClients", 1024 * 2 , (void*) 0, 1, NULL);
}
 
void loop() {
    websockets::WebsocketsClient client = server.accept();
    while (client.available()) {
        client.poll();
        fb = esp_camera_fb_get();
        client.sendBinary((const char *)fb->buf, fb->len);
        esp_camera_fb_return(fb);
        fb = NULL;

        delay(200);
    }
}

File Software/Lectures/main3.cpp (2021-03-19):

// Lekce 3 - rozhýbeme TrackRay, roztočíme motory, ukážeme číselnou proměnnou 
// a budeme regulovat rychlost motorů
#include "TrackRay/TrackRay.h"

int rychlost = 0;

void setup() {
    TrackRay.begin();
}

void loop() {
    bool tlacitko = trrReadButton();

    // Roztočení levého motoru pomocí konstrukce 'if'
    if(tlacitko) {
        trrMotorsSetSpeedLeft(50);
    }
    else {
        trrMotorsSetSpeedLeft(0);
    }

    //____________________________________________________
    // Postupné roztočení pravého motoru mačkáním tlačítka
    if(tlacitko) {
        rychlost = rychlost + 5;
    }
    else {
        rychlost = 0;
    }
    if(rychlost > 100) {
        rychlost = 100;
    }
    trrMotorsSetSpeedRight(rychlost);

    delay(100);
}
